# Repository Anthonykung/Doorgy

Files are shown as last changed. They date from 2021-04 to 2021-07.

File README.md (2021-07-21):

# Doorgy

A smart pet door for your smart home

***APLHA RELEASE WARNING*** Currently Under Development - This is not production ready!

Estimated Time of Completion: May 28, 2021

This is an open source academic group project for ECE 342 Junior Design at Oregon State University.

# Contents
- [Doorgy](#doorgy)
- [Contents](#contents)
  - [Overview](#overview)
  - [Prerequisite](#prerequisite)
    - [Doorgy Installation Package](#doorgy-installation-package)
    - [Required Software](#required-software)
    - [Configuring Doorgy Service](#configuring-doorgy-service)
      - [From GitHub](#from-github)
      - [From NPM](#from-npm)
  - [Install](#install)
    - [Physical Installation](#physical-installation)
    - [System Configuration](#system-configuration)
  - [License](#license)

## Overview

Doorgy is a smart pet door for your smart home. Control your pet door with nothing but your phone! Automated pet detection and door opening, say open sesame. Plug and play, no code required!

## Prerequisite

This project requires the Doorgy Installation Package that comes with the specific components require for the installation. Schematics of these components are available should you choose to create your own. You will not be able to proceed without these components.

Doorgy is part of the Doorgy Project, all parts of Doorgy Project are required to operate.

| Project | Registry | Repository |
| --- | --- | --- |
| Doorgy | [https://www.npmjs.com/package/doorgy](https://www.npmjs.com/package/doorgy) | [https://github.com/Anthonykung/Doorgy](https://github.com/Anthonykung/Doorgy) |
| Doorgy Server | | [https://github.com/Anthonykung/Doorgy-Server](https://github.com/Anthonykung/Doorgy-Server) |
| Doorgy App | | [https://github.com/Anthonykung/Doorgy-App](https://github.com/Anthonykung/Doorgy-App) |

### Doorgy Installation Package

- 1x Doorgy Printed Circuit Board
- 1x Raspberry Pi Zero WH
- 1x 16GB Doorgy Service Micro SD Card
- 2x HC-SR501
- 1x Doorgy LED Assembly
- 2x Servo Motors with Extended Arms
- 1x Battery Pack
- 1x Micro USB Power Supply
- 1x Doorgy Exterial Top/Bottom/Left/Right Frame
- 1x Doorgy Interial Top/Bottom/Left/Right Frame (Top frame comes with Circuit Housing)
- 1x Doorgy Door
- 1x Doorgy Door Connector & Doorgy Servo Connector
- 4x 1 Inch Doorgy Frame Screw
- 2x 1/4 Inch Doorgy Housing Screw
- 2x 1/4 Inch Doorgy Door Screw

### Required Software

If you have the Doorgy Service Micro SD Card, these has already been installed and configured.

If you do not have a Doorgy Service Micro SD Card, you will need a Micro SD Card with Raspbian Lite installed, more information available on [https://www.raspberrypi.org/documentation/installation/installing-images/](https://www.raspberrypi.org/documentation/installation/installing-images/). Once you have a Micro SD Card with Raspbian Lite installed, you can use the `doorgy-init.sh` located in `resources` folder of this repo to install the require softwares.

- UFW
- Fail2ban
- Git
- Node.js
- NPM
- Express.js
- mongoDB

Note: You should always secure your Raspberry Pi, Doorgy Service Micro SD Card will have security enabled by default. If you are using `doorgy-init.sh`, only firewall will be enabled. You will need to setup your Raspbian user and configure Fail2ban manually, more information available on [https://www.raspberrypi.org/documentation/configuration/security.md](https://www.raspberrypi.org/documentation/configuration/security.md)

### Configuring Doorgy Service

If you have the Doorgy Service Micro SD Card, these has already been installed and configured.

#### From GitHub

```
git clone https://github.com/Anthonykung/Doorgy.git
sudo npm install
sudo systemctl enable doorgy
```

If the installation fail, you can use `sudo npm run install` to try again. Sudo is required for all operations.

Once the service has been successfully configured, you can either start or reboot to start the service.

#### From NPM

```
mkdir ~/Doorgy
cd ~/Doorgy
sudo npm install doorgy
sudo systemctl enable doorgy
```

If the installation fail, you can use `sudo npm run install` to try again. Sudo is required for all operations.

Once the service has been successfully configured, you can either start or reboot to start the service.

## Install

This assume you have the Doorgy Installation Package and met all the prerequisites, if not please check that you have met the prerequisites before continuing.

### Physical Installation

1. Remove the door and place it on a table
2. Using the Doorgy Interial Frame, mark all 4 sides of the frame for cutting
3. Leave at least 3 inches of space on each side and 4 inches on the bottom
4. Cut the door on the marked location, this should give you a rectangular hole for the Doorgy Interial Frame
5. Place the Doorgy Interial Frame to the door (facing the inside), this should give you a tight fit
6. Place the Doorgy Exterial Frame on the other side overlapping the Doorgy Interial Frame
7. Using the 1 Inch Doorgy Screws, screw the Interial Fram to the Exterial Frame (the hole is located on the Interial Frame)
8. Using the 1/4 Inch Doorgy Screws, secure the circuit housing to the door (you will need to dril a 1/4 inch hole on the door)
9. On the exterial side, push the Doorgy Door in place with the hook on the top facing inside, secure it with the 1/4 inch screw to the frame
10. Attach the servo arm to the hook on top of the door, do not touch the servo arm on the left
11. Plugin the Micro USB power cable or attach 4x AAA batteries (not included) to the battery pack
12. Press the power up button and you are good to go! (Remember to tidy up the power cable so it doesn't get pulled out!)

### System Configuration

1. Install the Doorgy app on your smartphone
2. Open the Doorgy app and create an account
3. Setup WiFi connection with Raspberry Pi and run `npm run config`
4. Finish configuring Doorgy with the app
5. Once configuration is complete, follow the display to restart Doorgy (this is only needed during initial system configuration)
6. Enjoy your awesome new smart pet door!

## License

Copyright 2021 Doorgy Project Group

Licensed under the Apache License, Version 2.0 (the "License"); you may not use this file except in compliance with the License. You may obtain a copy of the License at

    http://www.apache.org/licenses/LICENSE-2.0

Unless required by applicable law or agreed to in writing, software distributed under the License is distributed on an "AS IS" BASIS, WITHOUT WARRANTIES OR CONDITIONS OF ANY KIND, either express or implied. See the License for the specific language governing permissions and limitations under the License.

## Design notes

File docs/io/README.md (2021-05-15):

# ECE 342 Pet Door Project - Doorgy

Doorgy - Smart Pet Door for your home, connected right to your phone. Hidden surprise included.

Created by Anthony Kung <hi@anth.dev> (https://anth.dev)

## Contents

- [ECE 342 Pet Door Project - Doorgy](#ece-342-pet-door-project---doorgy)
  - [Contents](#contents)
  - [Overview](#overview)
  - [Schematic](#schematic)
  - [Mechanical Drawing](#mechanical-drawing)
    - [Raspberry Pi Zero](#raspberry-pi-zero)
    - [HC-SR501](#hc-sr501)
    - [5mm LED](#5mm-led)
  - [Code](#code)
    - [Structure](#structure)
      - [Entire Service Package](#entire-service-package)
      - [Service File](#service-file)
    - [Primary Program Executable](#primary-program-executable)
    - [Installer](#installer)
    - [Service Scheduler](#service-scheduler)
  - [Block Diagrams](#block-diagrams)
    - [Overall System](#overall-system)
    - [Black Box Diagram](#black-box-diagram)
    - [Block Diagram](#block-diagram)
  - [Interface Definition](#interface-definition)
  - [Bill of Material](#bill-of-material)

## Overview

This portion of the project includes IR motion sensors and 5mm LEDs.

The IR sensors (HC-SR501) are used to detect pet movements from inside and outside the door. The IR sensor will be used to send the control signal to a single board computer (Raspberry Pi Zero WH) to be processed and activate the servo motors to open the door.

The 5mm LEDs are used to indicate the condition of the system. A green LED indicates the system is operating with sufficient power. A blue LED is used to indicate network connectivity. A red LED is used to indicate if the door has been locked. And a yellow LED is used to report errors. A 5mm LED has a current rating of 20mA, to protect the LED from the Raspberry Pi 5V voltage supply, a 250Ω resistor is required for each of them. This value is calculated by the formula ***V = IR*** where the resistor value can be found by dividing the voltage (5V) by the current (20mA) which gives 250Ω.

## Schematic

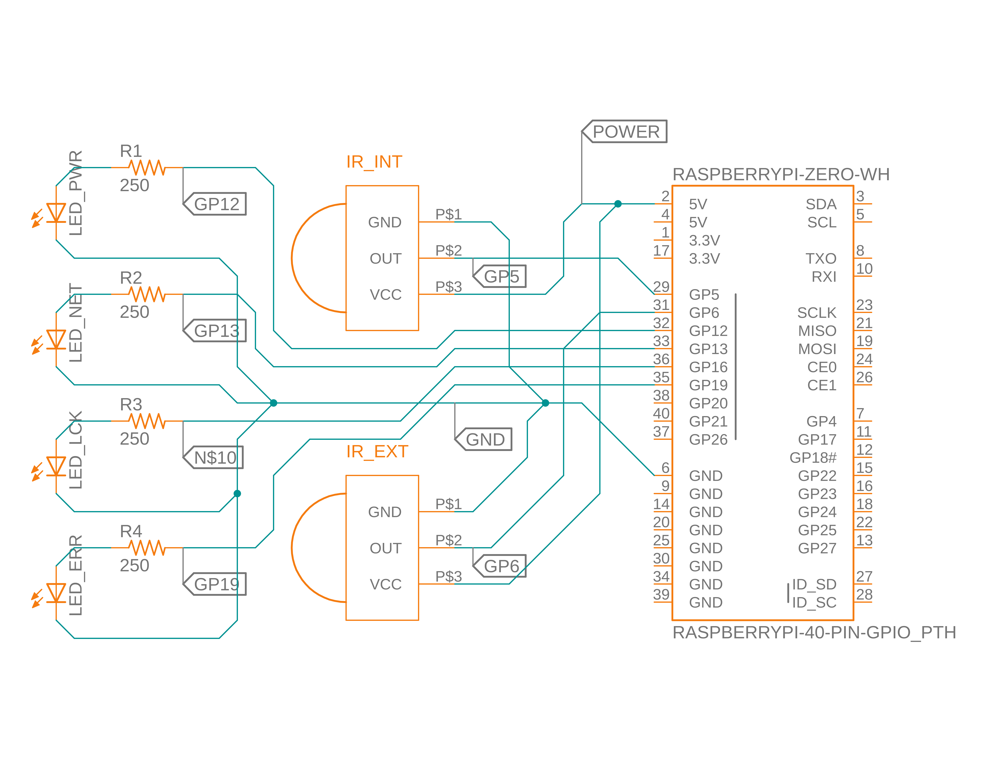
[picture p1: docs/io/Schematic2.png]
Schematic


## Mechanical Drawing

### Raspberry Pi Zero

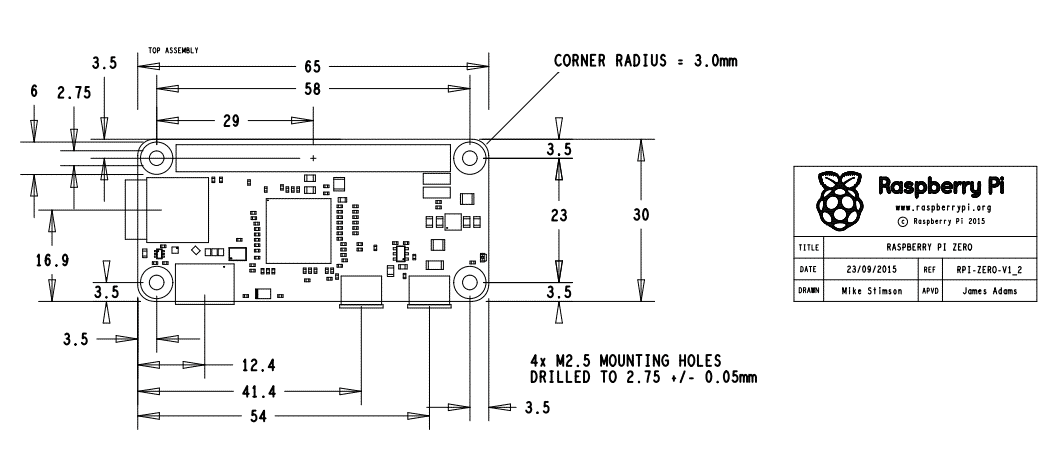
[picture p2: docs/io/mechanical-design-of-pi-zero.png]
Raspberry Pi Zero


### HC-SR501

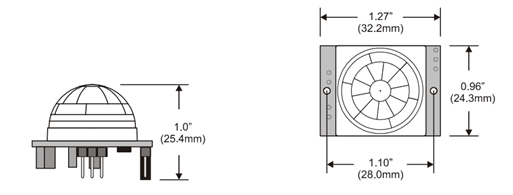
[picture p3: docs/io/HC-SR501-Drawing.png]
HC-SR501


### 5mm LED

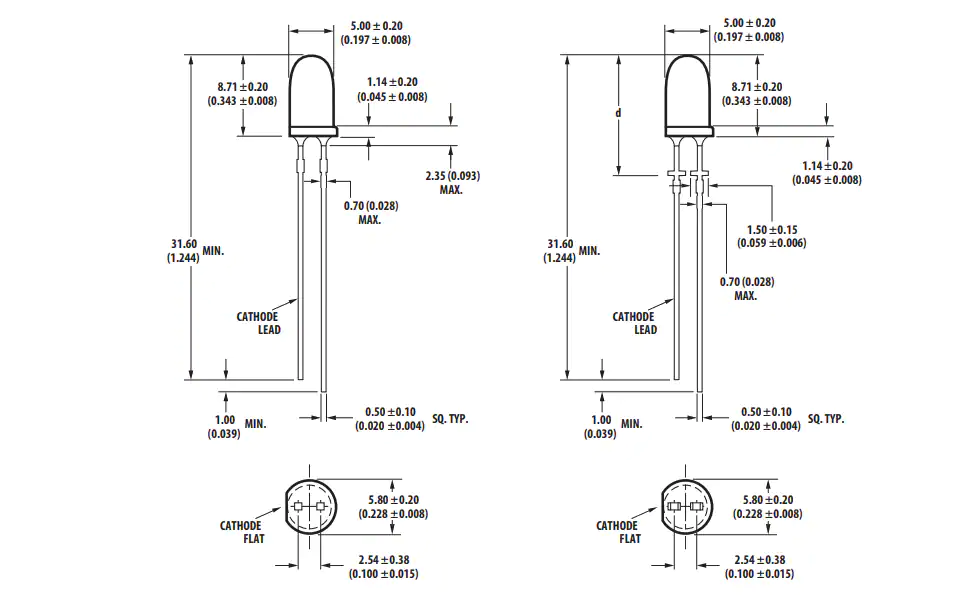
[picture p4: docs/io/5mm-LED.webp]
5mm LED


## Code

### Structure

#### Entire Service Package

```
/usr/local/src/
├── README.md
├── doorgy.js
├── package.json
└── resources/
    ├── installer.js
    ├── doorgy.service
    ├── doorgy-init.sh
    └── anthonian.js
```

#### Service File

```
/etc/systemd/services/
└── doorgy.service
```

### Primary Program Executable

```javascript
/**
 *
 * @description Doorgy - Smart Pet Door.
 * @file        doorgy.js
 * @link        https://doorgy.anth.dev
 * @license     Apache-2.0
 * @author      Anthony Kung <hi@anth.dev>
 * @since       1.0.0
 * @version     1.2.8
 *
 */

// Include Packages
const gpio = require('onoff').Gpio;
const fs = require('fs');
const anth = require('./resources/anthonian.js');
const { execSync, spawn } = require('child_process');
const http = require('http');

anth.anthdev();
anth.print('msg', 'Starting Doorgy Service');

// Define Global Constant
const server = 'doorgy.anth.dev';

// Define Global Variable
let ctrlSig = 1;
let printNum = 0;

// Define IR gpio
const IR_INT = new gpio(5, 'in', 'both');
const IR_EXT = new gpio(6, 'in', 'both');

// Define Buttons
const KILL = new gpio(20, 'in', 'rising', {debounceTimeout: 100});
const PSH_BTN2 = new gpio(21, 'in', 'rising', {debounceTimeout: 100});
const PSH_BTN3 = new gpio(26, 'in', 'rising', {debounceTimeout: 100});

// Define LED gpio
const LED_PWR = new gpio(12, 'out');
const LED_NET = new gpio(13, 'out');
const LED_LCK = new gpio(16, 'out');
const LED_ERR = new gpio(19, 'out');

anth.print('suc', 'GPIO Defined');
LED_PWR.writeSync(0);
LED_NET.writeSync(0);
LED_LCK.writeSync(0);
LED_ERR.writeSync(0);

// Turn on power indicator
LED_PWR.writeSync(1);

/**
 * Interial IR Function.
 *
 * @access private
 * @param  {*} err
 * @param  {*} value
 *
 * @memberof IR_INT
 */
IR_INT.watch((err, value) => {
  if (err) {
    throw err;
  }
  else if (value) {
    // Inform Servo Unit montion is detected
    console.log('IR_INT Sense', value);
    LED_ERR.writeSync(1);
  }
  else {
    // Inform Servo Unit no motion is detected
    console.log('IR_INT Not Sense', value);
    LED_ERR.writeSync(0);
  }
});

/**
 * Exterial IR Function.
 *
 * @access private
 * @param  {*} err
 * @param  {*} value
 *
 * @memberof IR_EXT
 */
IR_EXT.watch((err, value) => {
  if (err) {
    throw err;
  }
  else if (value) {
    // Inform Servo Unit montion is detected
    console.log('IR_EXT Sense', value);
    LED_ERR.writeSync(1);
  }
  else {
    // Inform Servo Unit no motion is detected
    console.log('IR_EXT Not Sense', value);
    LED_ERR.writeSync(0);
  }
});

/**
 * LED_LCK Test Function.
 *
 * @access private
 * @param  {*} err
 * @param  {*} value
 *
 * @memberof PSH_BTN2
 */
PSH_BTN2.watch((err, value) => {
  if (err) {
    throw err;
  }
  else if (value) {
    // Turn on Lock indicator
    console.log('Lock Sense', value);
    LED_LCK.writeSync(1);
    setTimeout(() => {
      console.log('Lock Release');
      LED_LCK.writeSync(0);
    }, 2000);
  }
  else {
    // Turn off Lock indicator
    console.log('Lock Not Sense', value);
    LED_LCK.writeSync(0);
  }
});

/**
 * LED_ERR Test Function.
 *
 * @access private
 * @param  {*} err
 * @param  {*} value
 *
 * @memberof PSH_BTN3
 */
PSH_BTN3.watch((err, value) => {
  if (err) {
    throw err;
  }
  else if (value) {
    // Turn on Lock indicator
    LED_ERR.writeSync(1);
  }
  else {
    // Turn off Lock indicator
    LED_ERR.writeSync(0);
  }
});

/**
 * Termination Cleanup Function.
 *
 * @name   clean
 * @access private
 * @param  {*} err
 * @param  {*} value
 */
function clean() {
  clearInterval(netCheck);
  LED_PWR.writeSync(1);
  LED_NET.writeSync(0);
  LED_LCK.writeSync(0);
  LED_ERR.writeSync(0);
  IR_INT.unexport();
  IR_EXT.unexport();
  LED_PWR.unexport();
  LED_NET.unexport();
  LED_LCK.unexport();
  LED_ERR.unexport();
}

/**
 * Interruption Control.
 *
 * Free resources and exit if interrupted.
 *
 * @listens SIGINT
 * @access private
 * @memberof process
 */
process.on('SIGINT', () => {
  clean();
  process.exit(0);
});

/**
 * Termination Control.
 *
 * Free resources and exit if terminated.
 *
 * @listens SIGTERM
 * @access private
 * @memberof process
 */
process.on('SIGTERM', () => {
  clean();
  process.exit(0);
});

/**
 * Locking Control.
 *
 * Listern for Locking Mechnism.
 *
 * @listens message
 * @access private
 * @memberof process
 */
process.on('message', message => {
  let comm = JSON.parse(message);
  if (comm.Lock.status == 1) {
    // Turn on Lock indicator
    LED_LCK.writeSync(1);
  }
  else {
    // Turn off Lock indicator
    LED_LCK.writeSync(0);
  }
});

anth.print('msg', 'Starting Operation');

/**
 * Network Check Function.
 *
 * Check for network connection.
 *
 * @name   checkNetwork
 * @access private
 * @param  {string} server
 */
function checkNetwork(server) {
  let  options = {
    host: server,
    path: '/'
  };
  http.get(options, (res) => {
    if (!printNum) {
      anth.print('suc', 'Connection Established');
      printNum++;
    }
    LED_NET.writeSync(1);
  }).on('error', function(error) {
    console.error('Error Detected:', error);
    LED_NET.writeSync(0);
    LED_ERR.writeSync(1);
    anth.print('err', 'Unable to communicate with server');
  });
}

let netCheck = setInterval(checkNetwork(server), 100);

/**
 * Kill Function.
 *
 * Initiate graceful shutdown
 *
 * @access private
 * @param  {*} err
 * @param  {*} value
 *
 * @memberof KILL
 */
KILL.watch((err, value) => {
  if (err) {
    throw err;
  }
  else if (value) {
    clean();
    let cmd = execSync('shutdown -h now');
  }
  else {
    console.error('Error Detected:', error);
    LED_ERR.writeSync(1);
    anth.print('err', 'Unable to shutdown the server');
  }
});
```

### Installer

```js
#!/usr/bin/env node

/*******************************************
 *                                         *
 * Name: installer.js                      *
 * Description: Doorgy Installation Helper *
 * Date: April 26, 2021                    *
 * Created by: Anthony Kung                *
 * Author URL: https://anth.dev            *
 * License: Apache-2.0 (See LICENSE.md)    *
 *                                         *
 *******************************************/

// Just to be nice
'use strict';

// Modules
const { exec, spawn } = require('child_process');
const anth = require('./anthonian.js');
const fs = require("fs");
const path = require('path');
const fse = require('fs-extra');

anth.print('msg', 'Checking Directory Location');

if (__dirname != '/usr/local/src/doorgy') {
  anth.print('msg', 'Relocation required, relocating...');
  try {
    fse.copySync(__dirname + '/../', '/usr/local/src/doorgy');
    anth.print('suc', 'Relocation Success');
  } catch (err) {
    anth.print('err', 'Unable to move directory');
  }
}
anth.print('suc', 'Directory Check Completed');

anth.print('msg', 'Checking Service Location');

if (!fs.existsSync('/etc/systemd/system/doorgy.service')) {
  anth.print('msg', 'Service not found, adding service...');
  try {
    fse.copySync(path.join(__dirname, 'doorgy.service'), '/etc/systemd/system/doorgy.service');
    anth.print('suc', 'Service Added Successfully');
  } catch (err) {
    anth.print('err', 'Unable to move file');
  }
}
anth.print('suc', 'Service Check Completed');

anth.print('suc', 'Doorgy Installation Completed');
anth.print('msg', ['Start the service using', anth.pink, 'sudo npm start', anth.blue, 'or', anth.pink, 'sudo systemctl start doorgy.service', anth.blue, 'sudo is required for system services']);
```

### Service Scheduler

```
[Unit]
Description=Doorgy Service Agent
Documentation=https://github.com/Anthonykung/Doorgy

[Service]
ExecStart=/usr/bin/node /usr/local/src/doorgy/doorgy.js
WorkingDirectory=/usr/local/src/doorgy
StandardOutput=inherit
StandardError=inherit
Restart=always
User=root

[Install]
WantedBy=multi-user.target
```

## Block Diagrams

### Overall System

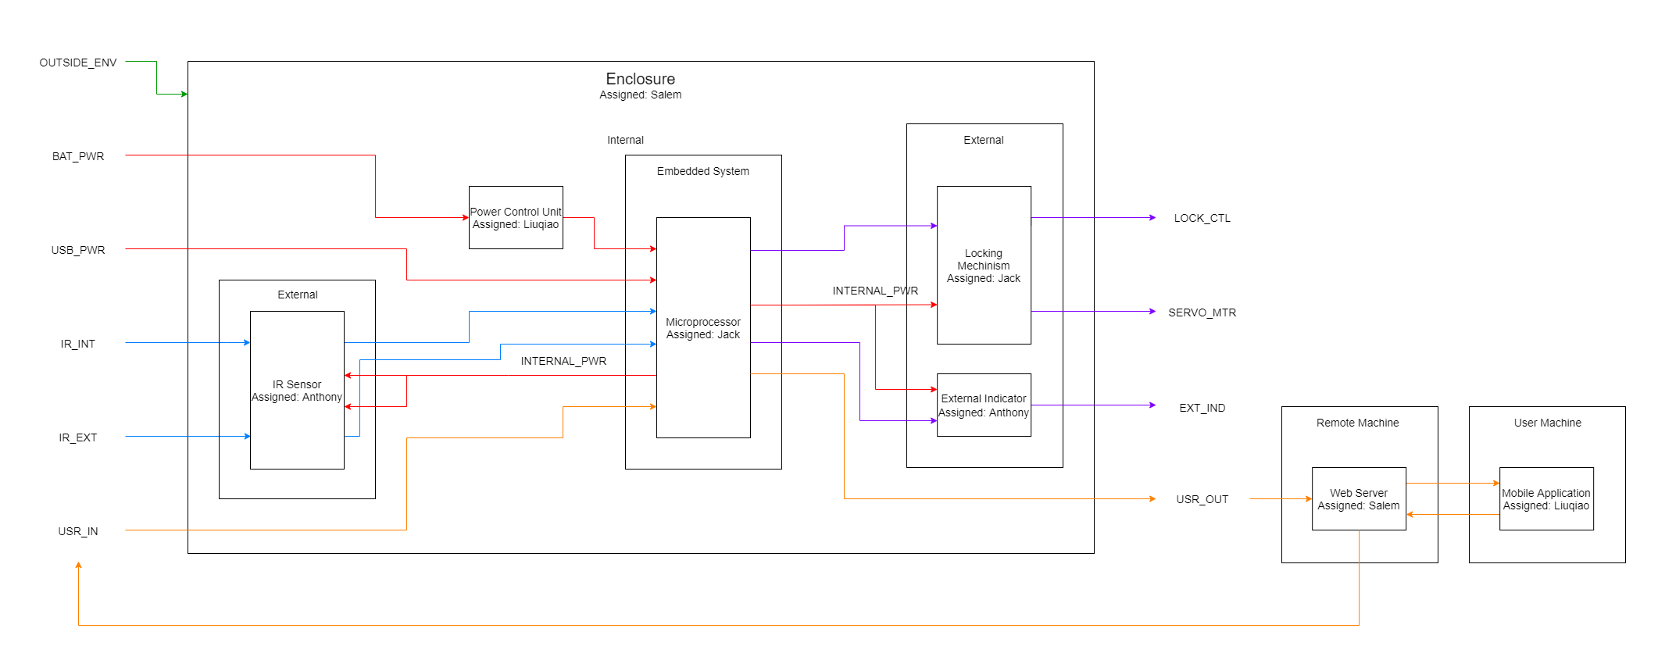
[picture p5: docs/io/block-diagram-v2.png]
Overall Block Diagram


### Black Box Diagram
Black Box Diagram

### Block Diagram
Block Diagram

## Interface Definition

| Name | Type | Definition |
| --- | --- | --- |
| BAT_PWR  | DC Power | <ul><li>Voltage: 5.1V</li><li>Current: 1.2A</li></ul> |
| USB_PWR  | DC Power | <ul><li>Voltage: 5.1V</li><li>Current: 1.2A</li></ul> |
| POWER | DC Power | <ul><li>Voltage: 5.0V</li><li>Current: 1.2A</li></ul> |
| IR_INT | Analog Signal | <ul><li>Voltage: DC 5V</li><li>Minimium Range: 1m</li></ul> |
| IR_EXT | Analog Signal | <ul><li>Voltage: DC 5V</li><li>Minimium Range: 1m</li></ul> |
| COMM_IN  | Data | Format: JSON Object |
| COMM_OUT | Data | Format: JSON Object |
| LED_PWR  | Analog Signal | <ul><li>Voltage: 5.0V</li><li>Current: 20mA</li></ul> |
| LED_NET  | Analog Signal | <ul><li>Voltage: 5.0V</li><li>Current: 20mA</li></ul> |
| LED_LCK  | Analog Signal | <ul><li>Voltage: 5.0V</li><li>Current: 20mA</li></ul> |
| LED_ERR  | Analog Signal | <ul><li>Voltage: 5.0V</li><li>Current: 20mA</li></ul> |

## Bill of Material

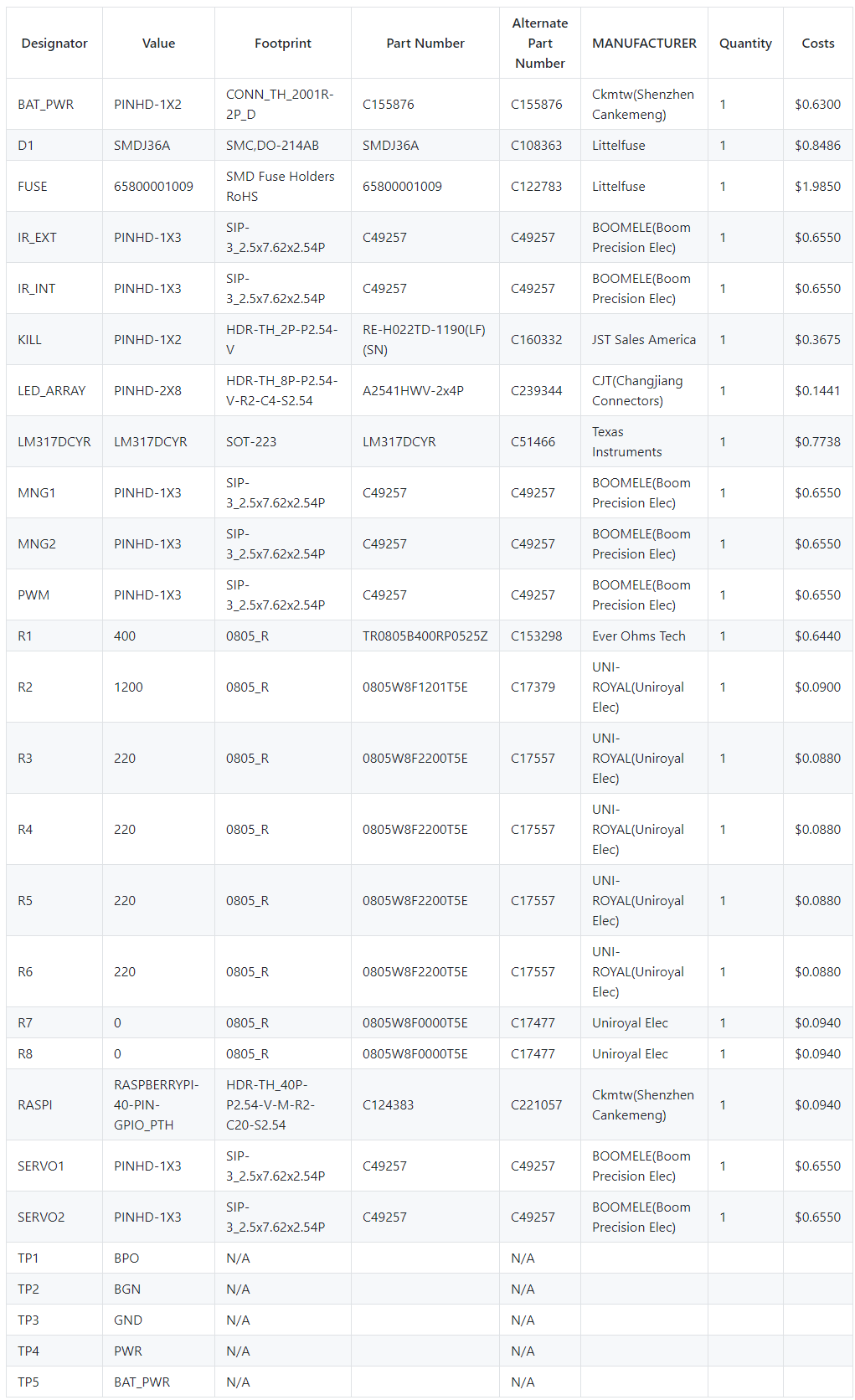
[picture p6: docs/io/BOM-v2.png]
BOM


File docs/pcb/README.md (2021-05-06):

# Doorgy PCB

The Doorgy PCB integrates Raspberry Pi Zero WH with the Doorgy Frame and Hardwares.

Schematics, PCB Layout and Gerber Files are open source and freely available on this directory.

BOM and CPL used to construct Doorgy PCB on JLCPCB is also available on this directory.

- [Doorgy PCB](#doorgy-pcb)
  - [Gerber Files](#gerber-files)
  - [BOM](#bom)
  - [CPL](#cpl)
  - [PCB](#pcb)
  - [Schematic](#schematic)
  - [Layout](#layout)

## Gerber Files

Current version: v33

Gerber files of the Doorgy PCB is located at [./Doorgy-PCB_2021-05-04-v33.zip](./Doorgy-PCB_2021-05-04-v33.zip)

## BOM

The BOM is currently only available in Microsoft Excel format and is located at [./Doorgy-PCB-BOM.xlsx](./Doorgy-PCB-BOM.xlsx)

## CPL

The CPL is currently only available in Microsoft Excel format and is located at [./Doorgy-PCB-CPL.xlsx](./Doorgy-PCB-CPL.xlsx)

## PCB

This is a illustration of a constructed Doorgy PCB Layout Version 32

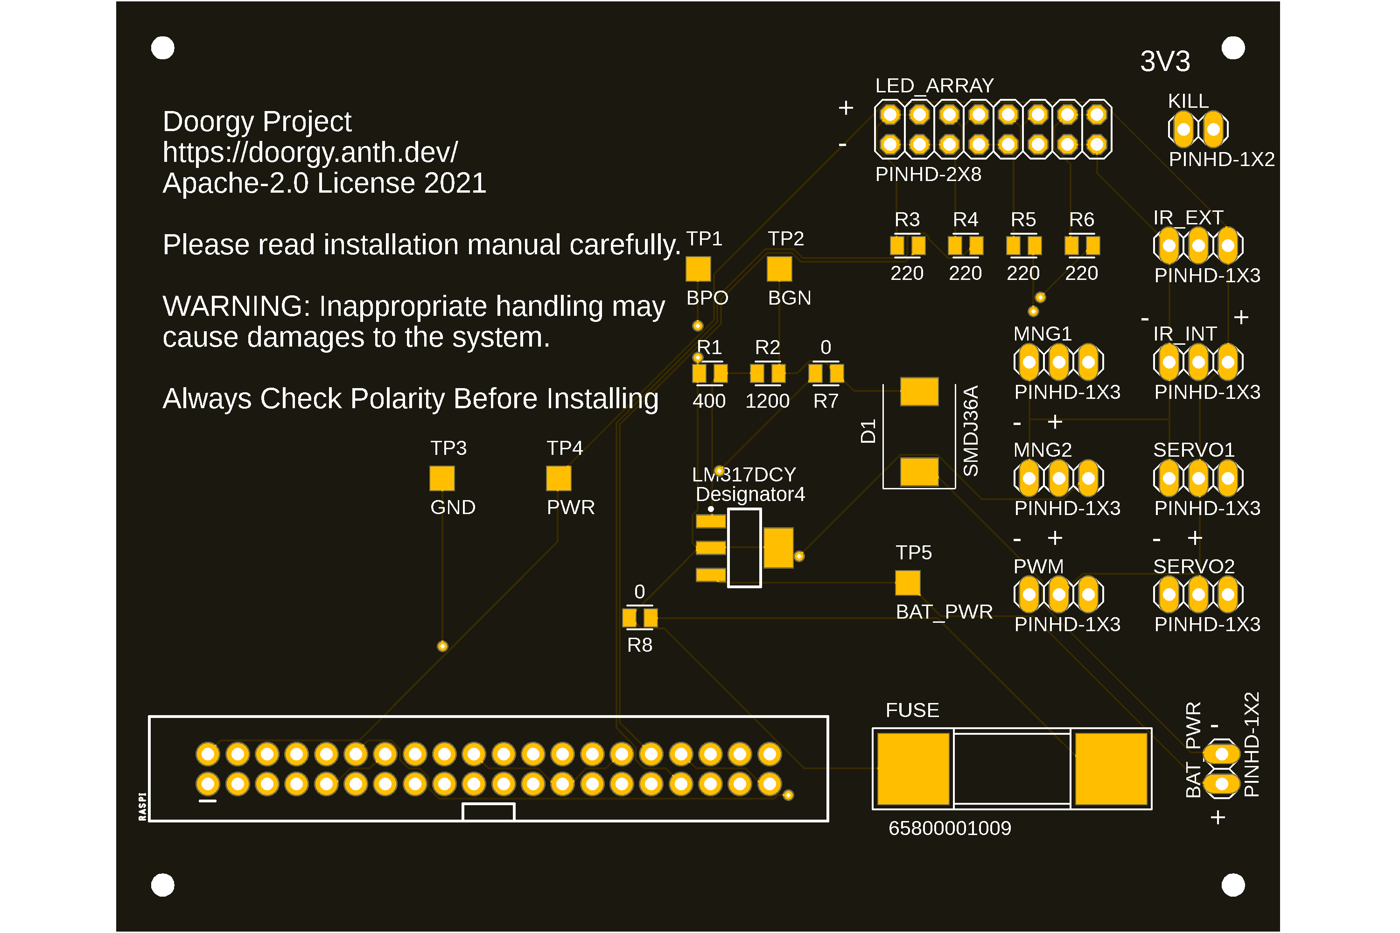
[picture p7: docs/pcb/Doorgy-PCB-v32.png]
Doorgy PCB v32


## Schematic

This is the schematic of Doorgy PCB Schematic Version 22, note that resistor values have been changed to accomodate the parts available at JLCPCB.

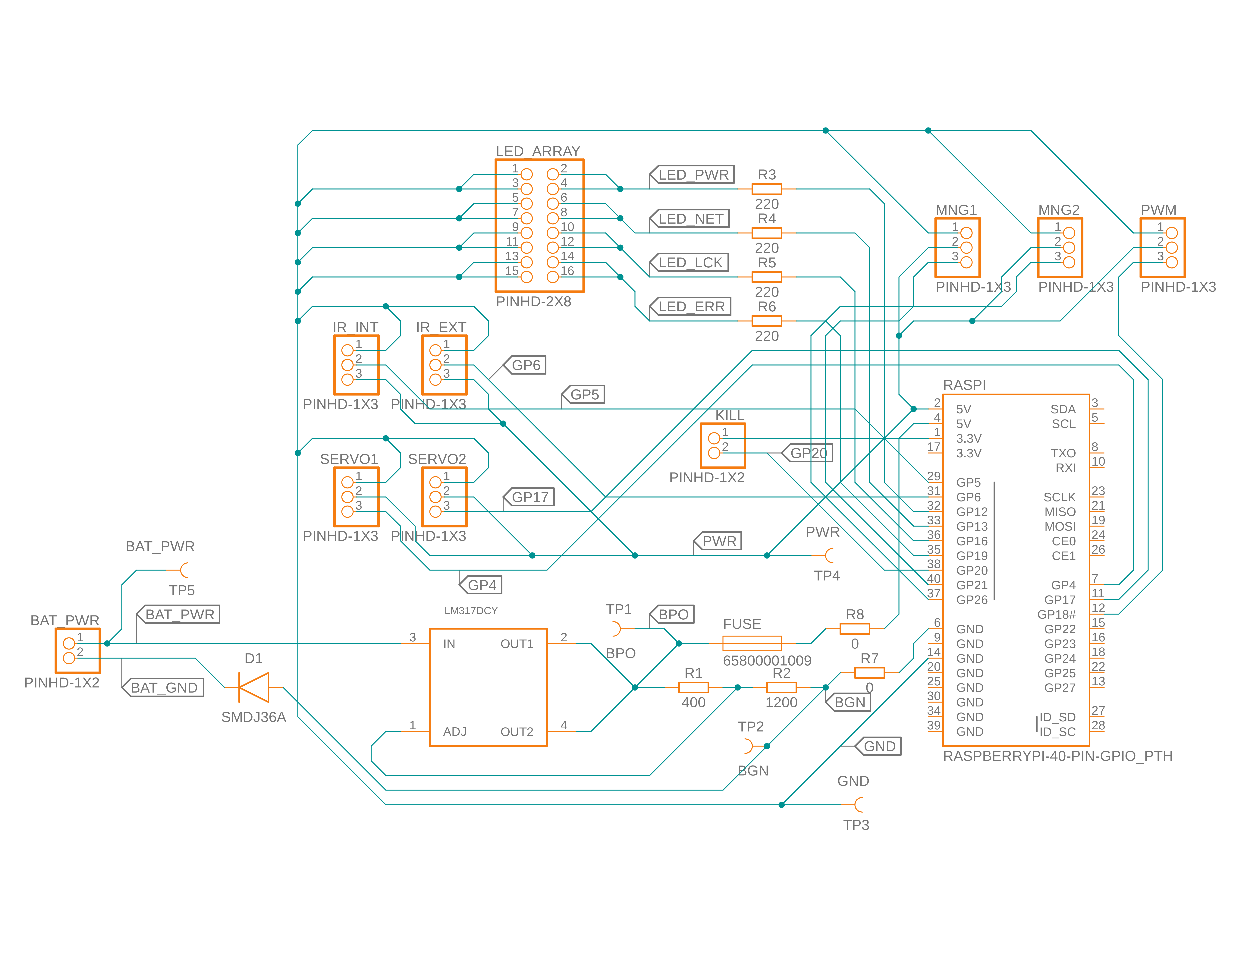
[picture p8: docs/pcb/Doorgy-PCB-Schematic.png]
Schematic v22


## Layout

This is the routing layout of Doorgy PCB Layout Version 32.

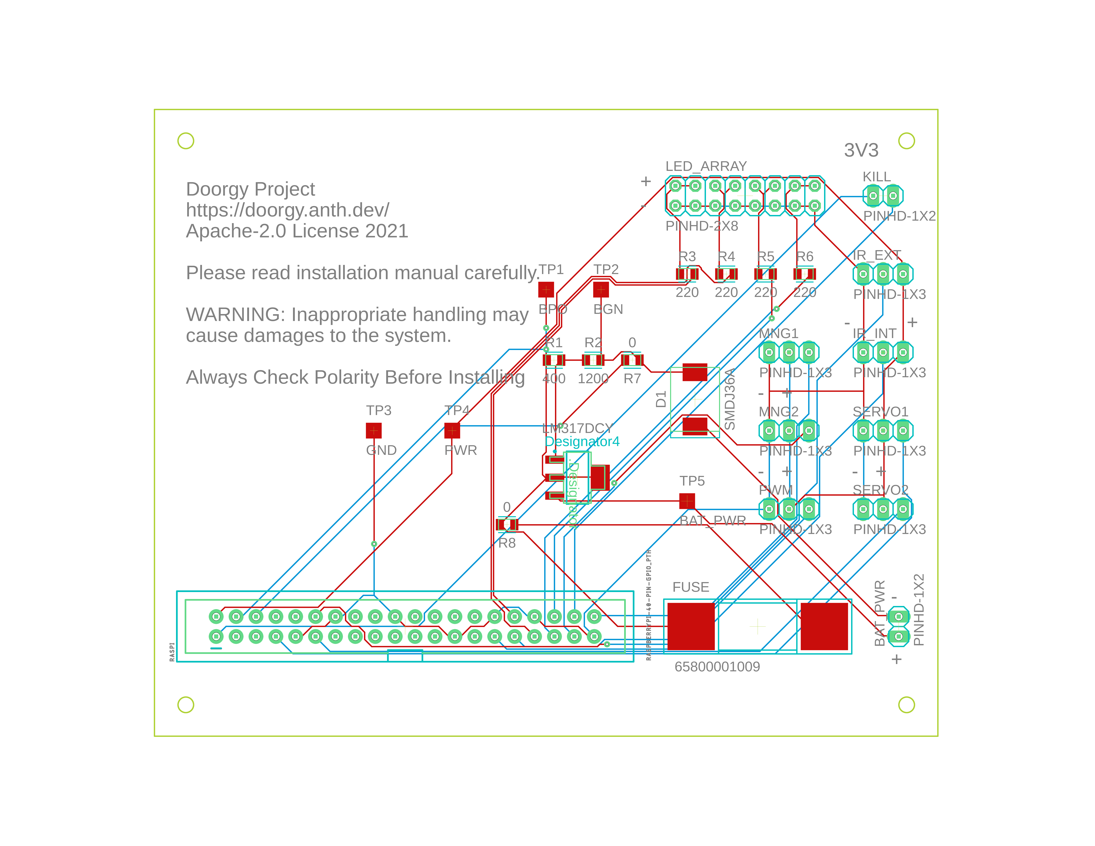
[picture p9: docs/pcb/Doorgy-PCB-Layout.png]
Layout v32


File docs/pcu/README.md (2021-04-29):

# Power Control Unit

This block is managed by Liuqiao Song

## Contents
- [Power Control Unit](#power-control-unit)
  - [Contents](#contents)
  - [Schematic](#schematic)
  - [Bill of Material](#bill-of-material)
  - [Additional](#additional)
    - [Voltage Monitoring](#voltage-monitoring)

## Schematic

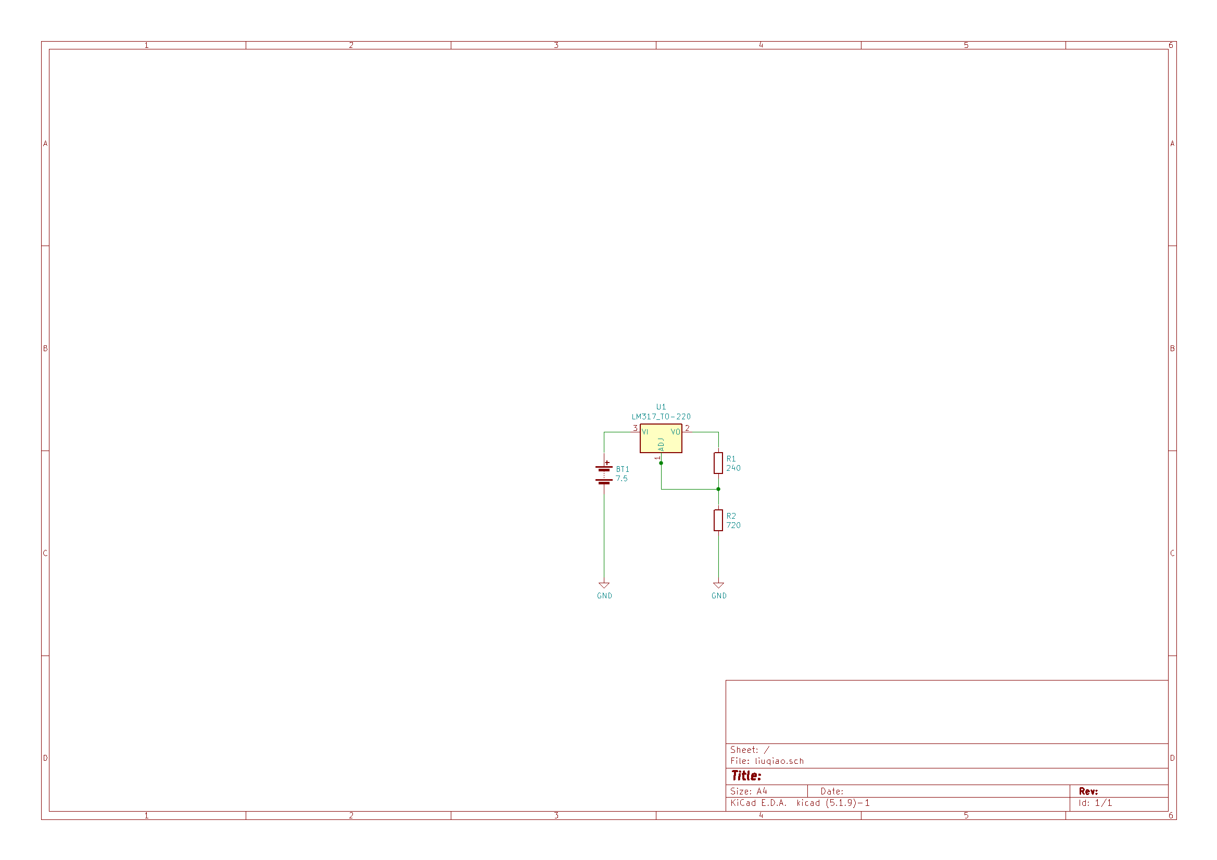
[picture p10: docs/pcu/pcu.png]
Power Control Unit


## Bill of Material

| Quantity | Name |
| --- | --- |
| 1 | LM317 |
| 1 | 240 ohm R |
| 1 | 720 ohm R |
| 1 | 5 pack AA battery |

## Additional

This section is added by Anthony Kung

### Voltage Monitoring

An INA 169 will be used to monitor voltage and provide battery statistics to the Raspi. AA battery operates at 1.5V and became inoperatable at around 1.2V.

[INA169 Datasheet](https://www.ti.com/lit/ds/symlink/ina169.pdf)

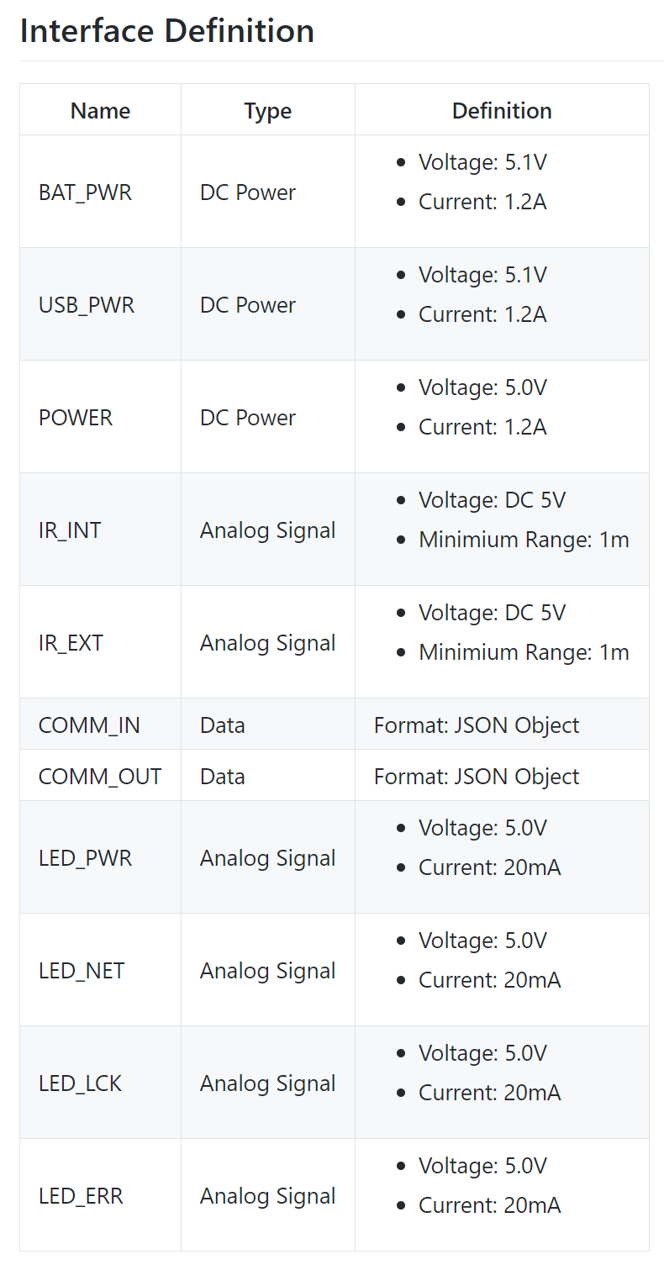
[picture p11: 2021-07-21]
docs/overview/Screenshot 2021-05-28 204917.png

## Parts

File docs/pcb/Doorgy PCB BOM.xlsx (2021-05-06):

Comment | Designator | Footprint | LCSC Part #（optional）
PINHD-1X2 | BAT_PWR | CONN_TH_2001R-2P_D | C155876
SMDJ36A | D1 | SMC,DO-214AB | C108363
65800001009 | FUSE | SMD Fuse Holders RoHS | C122783
PINHD-1X3 | IR_EXT | SIP-3_2.5x7.62x2.54P | C49257
PINHD-1X3 | IR_INT | SIP-3_2.5x7.62x2.54P | C49257
PINHD-1X2 | KILL | HDR-TH_2P-P2.54-V | C160332
PINHD-2X8 | LED_ARRAY | HDR-TH_8P-P2.54-V-R2-C4-S2.54 | C239344
LM317DCYR | LM317DCYR | SOT-223 | C51466
PINHD-1X3 | MNG1 | SIP-3_2.5x7.62x2.54P | C49257
PINHD-1X3 | MNG2 | SIP-3_2.5x7.62x2.54P | C49257
PINHD-1X3 | PWM | SIP-3_2.5x7.62x2.54P | C49257
400 | R1 | 0805_R | C153298
1200 | R2 | 0805_R | C17379
220 | R3 | 0805_R | C17557
220 | R4 | 0805_R | C17557
220 | R5 | 0805_R | C17557
220 | R6 | 0805_R | C17557
0 | R7 | 0805_R | C17477
0 | R8 | 0805_R | C17477
RASPBERRYPI-40-PIN-GPIO_PTH | RASPI | HDR-TH_40P-P2.54-V-M-R2-C20-S2.54 | C221057
PINHD-1X3 | SERVO1 | SIP-3_2.5x7.62x2.54P | C49257
PINHD-1X3 | SERVO2 | SIP-3_2.5x7.62x2.54P | C49257
Leave Empty | TP1 | N/A | N/A
Leave Empty | TP2 | N/A | N/A
Leave Empty | TP3 | N/A | N/A
Leave Empty | TP4 | N/A | N/A
Leave Empty | TP5 | N/A | N/A

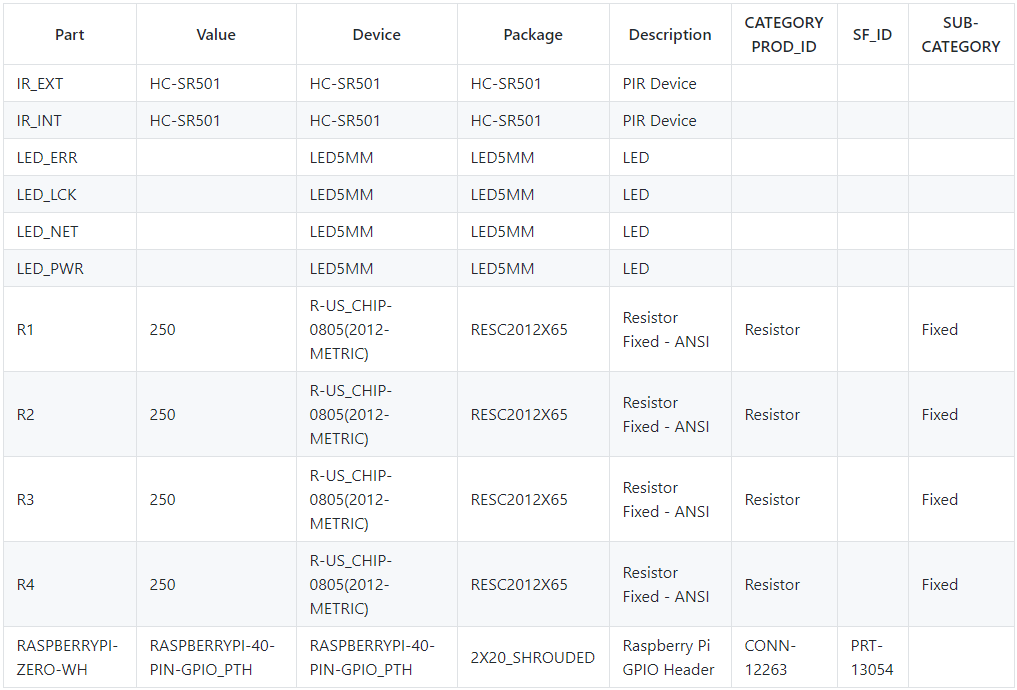
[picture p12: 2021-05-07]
docs/io/BOM.png

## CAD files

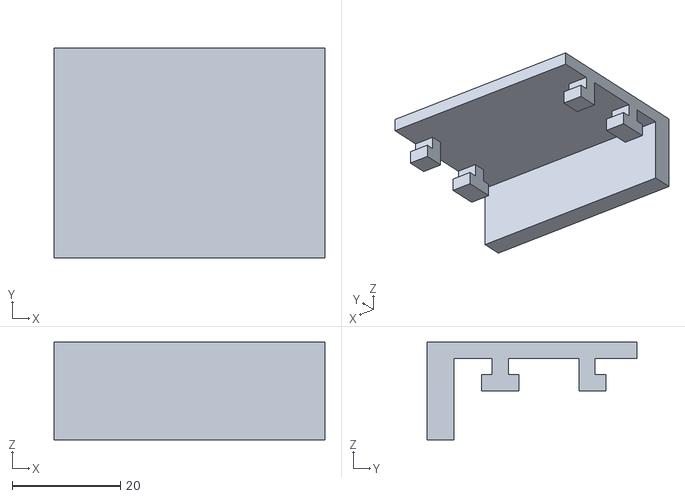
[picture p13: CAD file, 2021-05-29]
Doorgy Physical STL/Doorgy Exterial Top Cover.stl
50.0 x 38.8 x 18.0

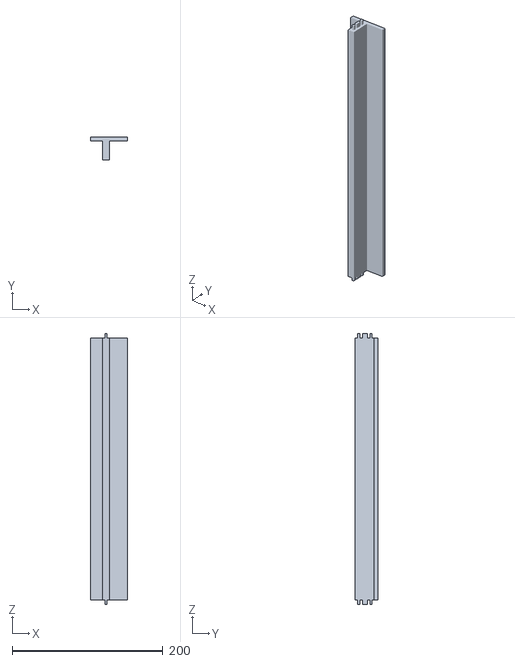
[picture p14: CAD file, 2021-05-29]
Doorgy Physical STL/Doorgy Exterial Left Frame.stl
49.0 x 30.4 x 359.0

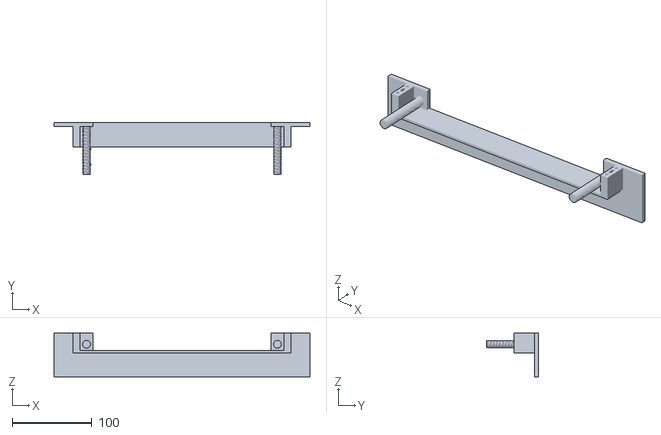
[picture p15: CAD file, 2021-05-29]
Doorgy Physical STL/Doorgy Exterial Bottom Frame.stl
322.0 x 65.0 x 55.0

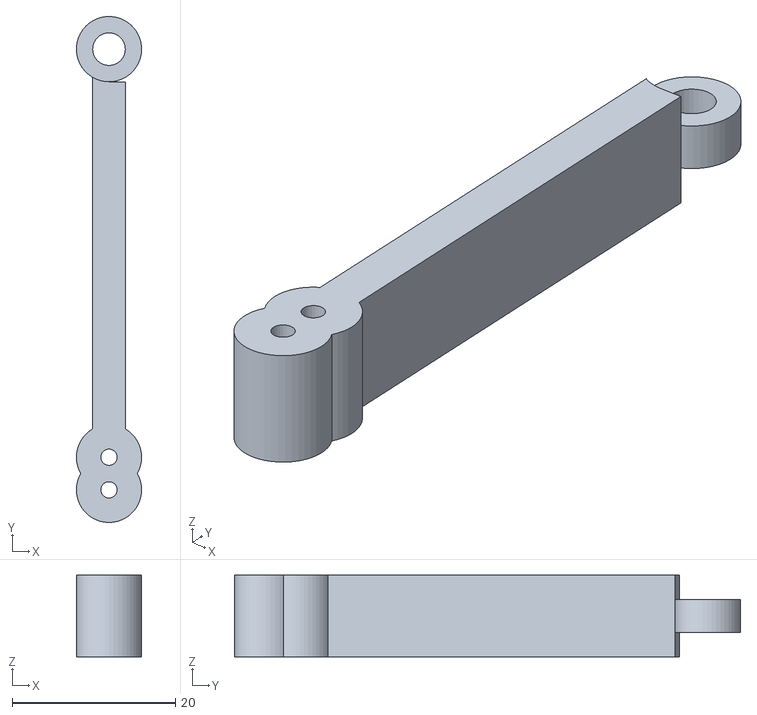
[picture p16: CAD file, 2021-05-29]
Doorgy Physical STL/Doorgy Servo Connector.stl
8.00 x 62.0 x 10.0

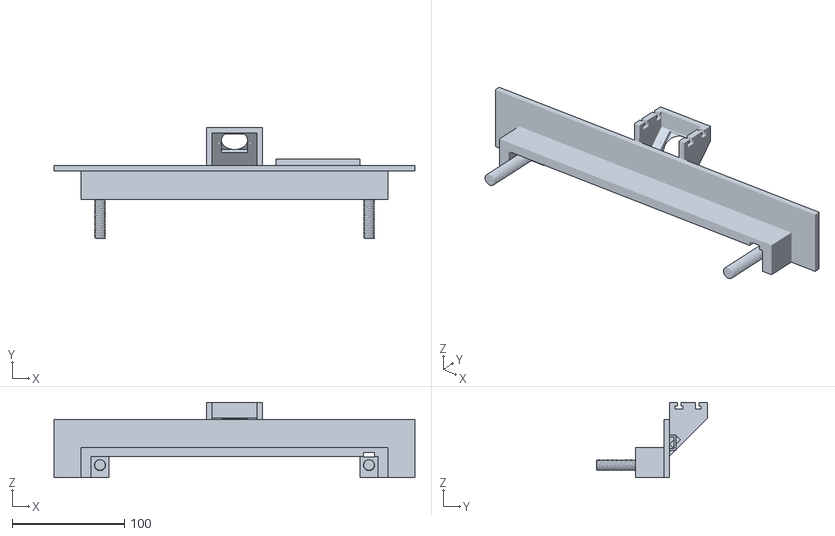
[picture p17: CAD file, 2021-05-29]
Doorgy Physical STL/Doorgy Exterial Top Frame.stl
322.0 x 98.9 x 67.0

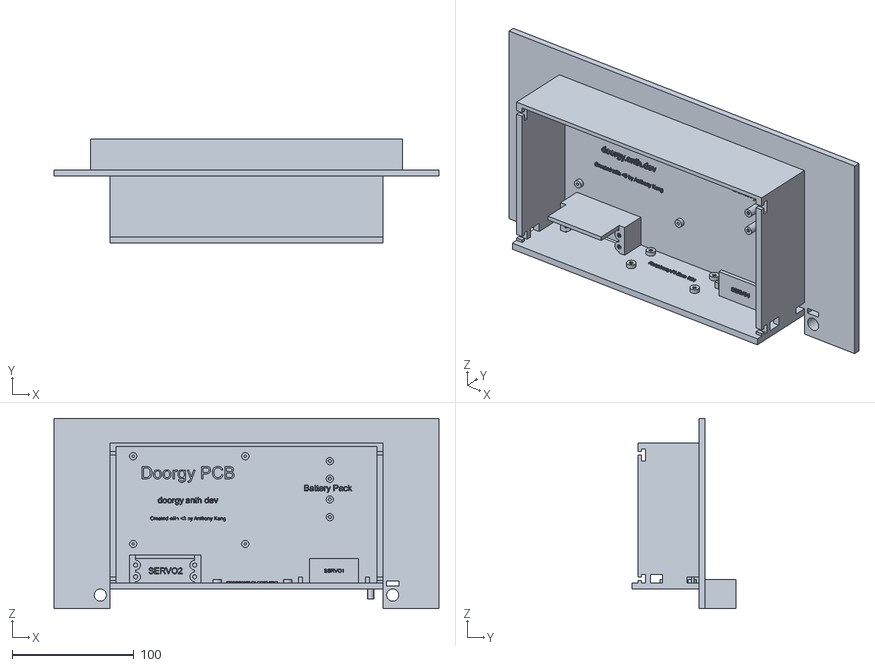
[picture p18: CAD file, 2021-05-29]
Doorgy Physical STL/Doorgy Interial Top Frame.stl
316.0 x 85.4 x 156.0

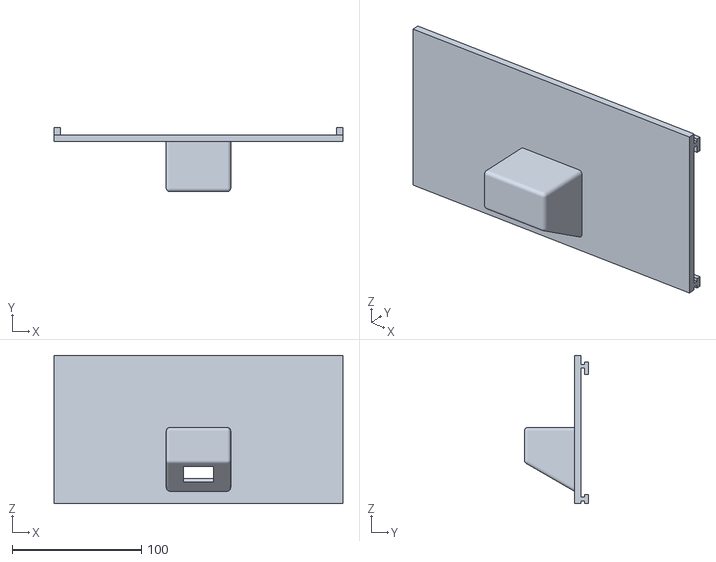
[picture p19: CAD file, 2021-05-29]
Doorgy Physical STL/Doorgy Interial Top Cover.stl
224.0 x 49.8 x 115.0

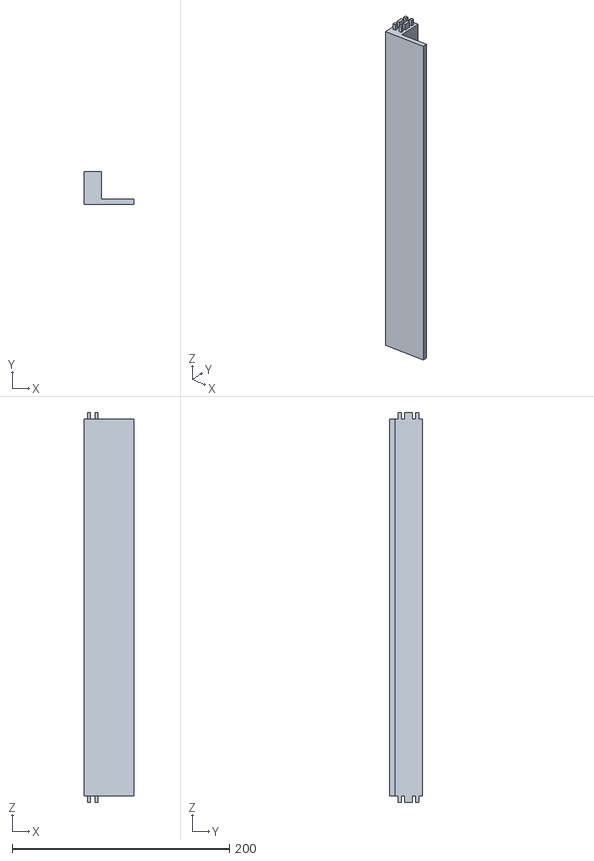
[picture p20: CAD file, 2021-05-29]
Doorgy Physical STL/Doorgy Interial Right Frame.stl
46.0 x 30.4 x 359.0

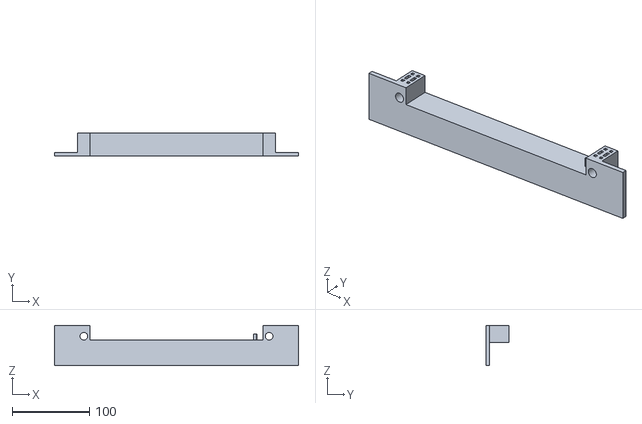
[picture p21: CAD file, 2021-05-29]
Doorgy Physical STL/Doorgy Interial Bottom Frame.stl
316.0 x 30.4 x 52.0

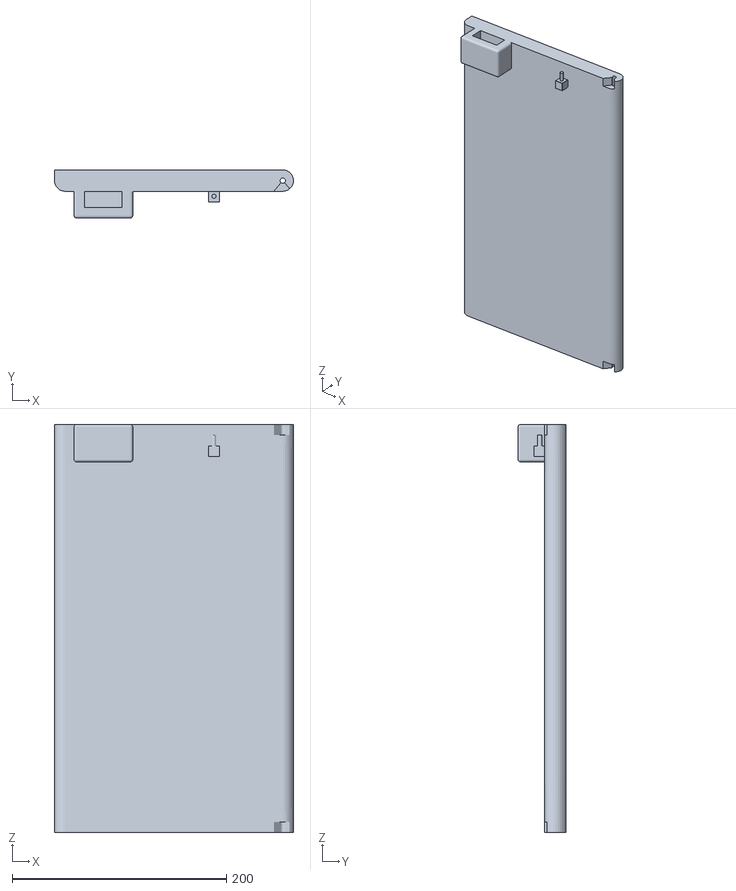
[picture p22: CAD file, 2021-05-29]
Doorgy Physical STL/Doorgy Door.stl
223.2 x 45.0 x 381.0

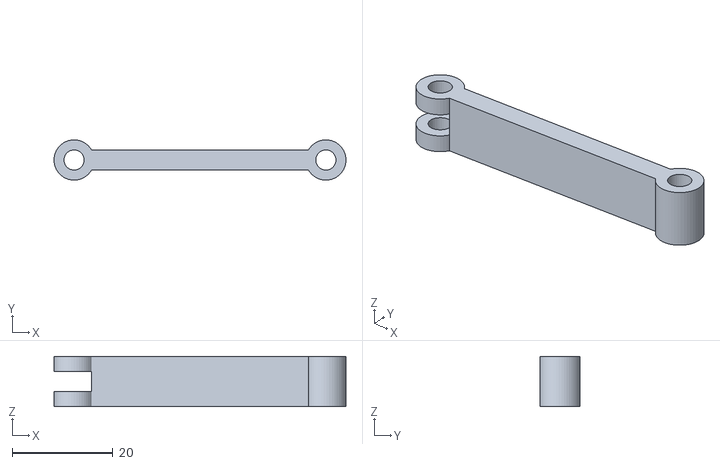
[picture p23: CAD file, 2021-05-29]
Doorgy Physical STL/Doorgy Door Connector.stl
58.0 x 8.00 x 10.0

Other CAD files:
Doorgy Physical STL/Doorgy Exterial Right Frame.stl
Doorgy Physical STL/Doorgy Interial Left Frame.stl

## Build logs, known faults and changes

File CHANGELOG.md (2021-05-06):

# Doorgy Change Log

- [Doorgy Change Log](#doorgy-change-log)
  - [v1.2.7](#v127)
  - [v1.2.6](#v126)
  - [v1.2.5](#v125)
  - [v1.2.4](#v124)
  - [v1.2.3](#v123)
  - [v1.2.2](#v122)
  - [v1.2.1](#v121)
  - [v1.2.0](#v120)
  - [v1.1.0](#v110)
  - [v1.0.0](#v100)

## v1.2.7

- Fix PCB Layout Drill Layer
- Fix PCB BOM Raspberry Pi Header
- Update README

## v1.2.6

- Update PCB Schematics and Layout

## v1.2.5

- Added draft PCB Schematics and Layout
- Added CHANGELOG.md

## v1.2.4

## v1.2.3

## v1.2.2

## v1.2.1

## v1.2.0

## v1.1.0

## v1.0.0

- Initial release
- Added doorgy.js

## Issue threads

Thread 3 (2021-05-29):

Project name might be misinterpreted

TheOneKevin, 2021-05-29:
The name Doorgy may be misinterpreted as the slang term "doorgy" may also have unpleasant and vulgar connotations. Instead, Doorgi might be a better alternative as it can be Door + Corgi.

Anthonykung, 2021-05-30:
Yes, we are aware of this issue however, that is after the PCB was created making the changes hard to implement. Changes will be made on 3.0.0 updates along with a new NPM listing.

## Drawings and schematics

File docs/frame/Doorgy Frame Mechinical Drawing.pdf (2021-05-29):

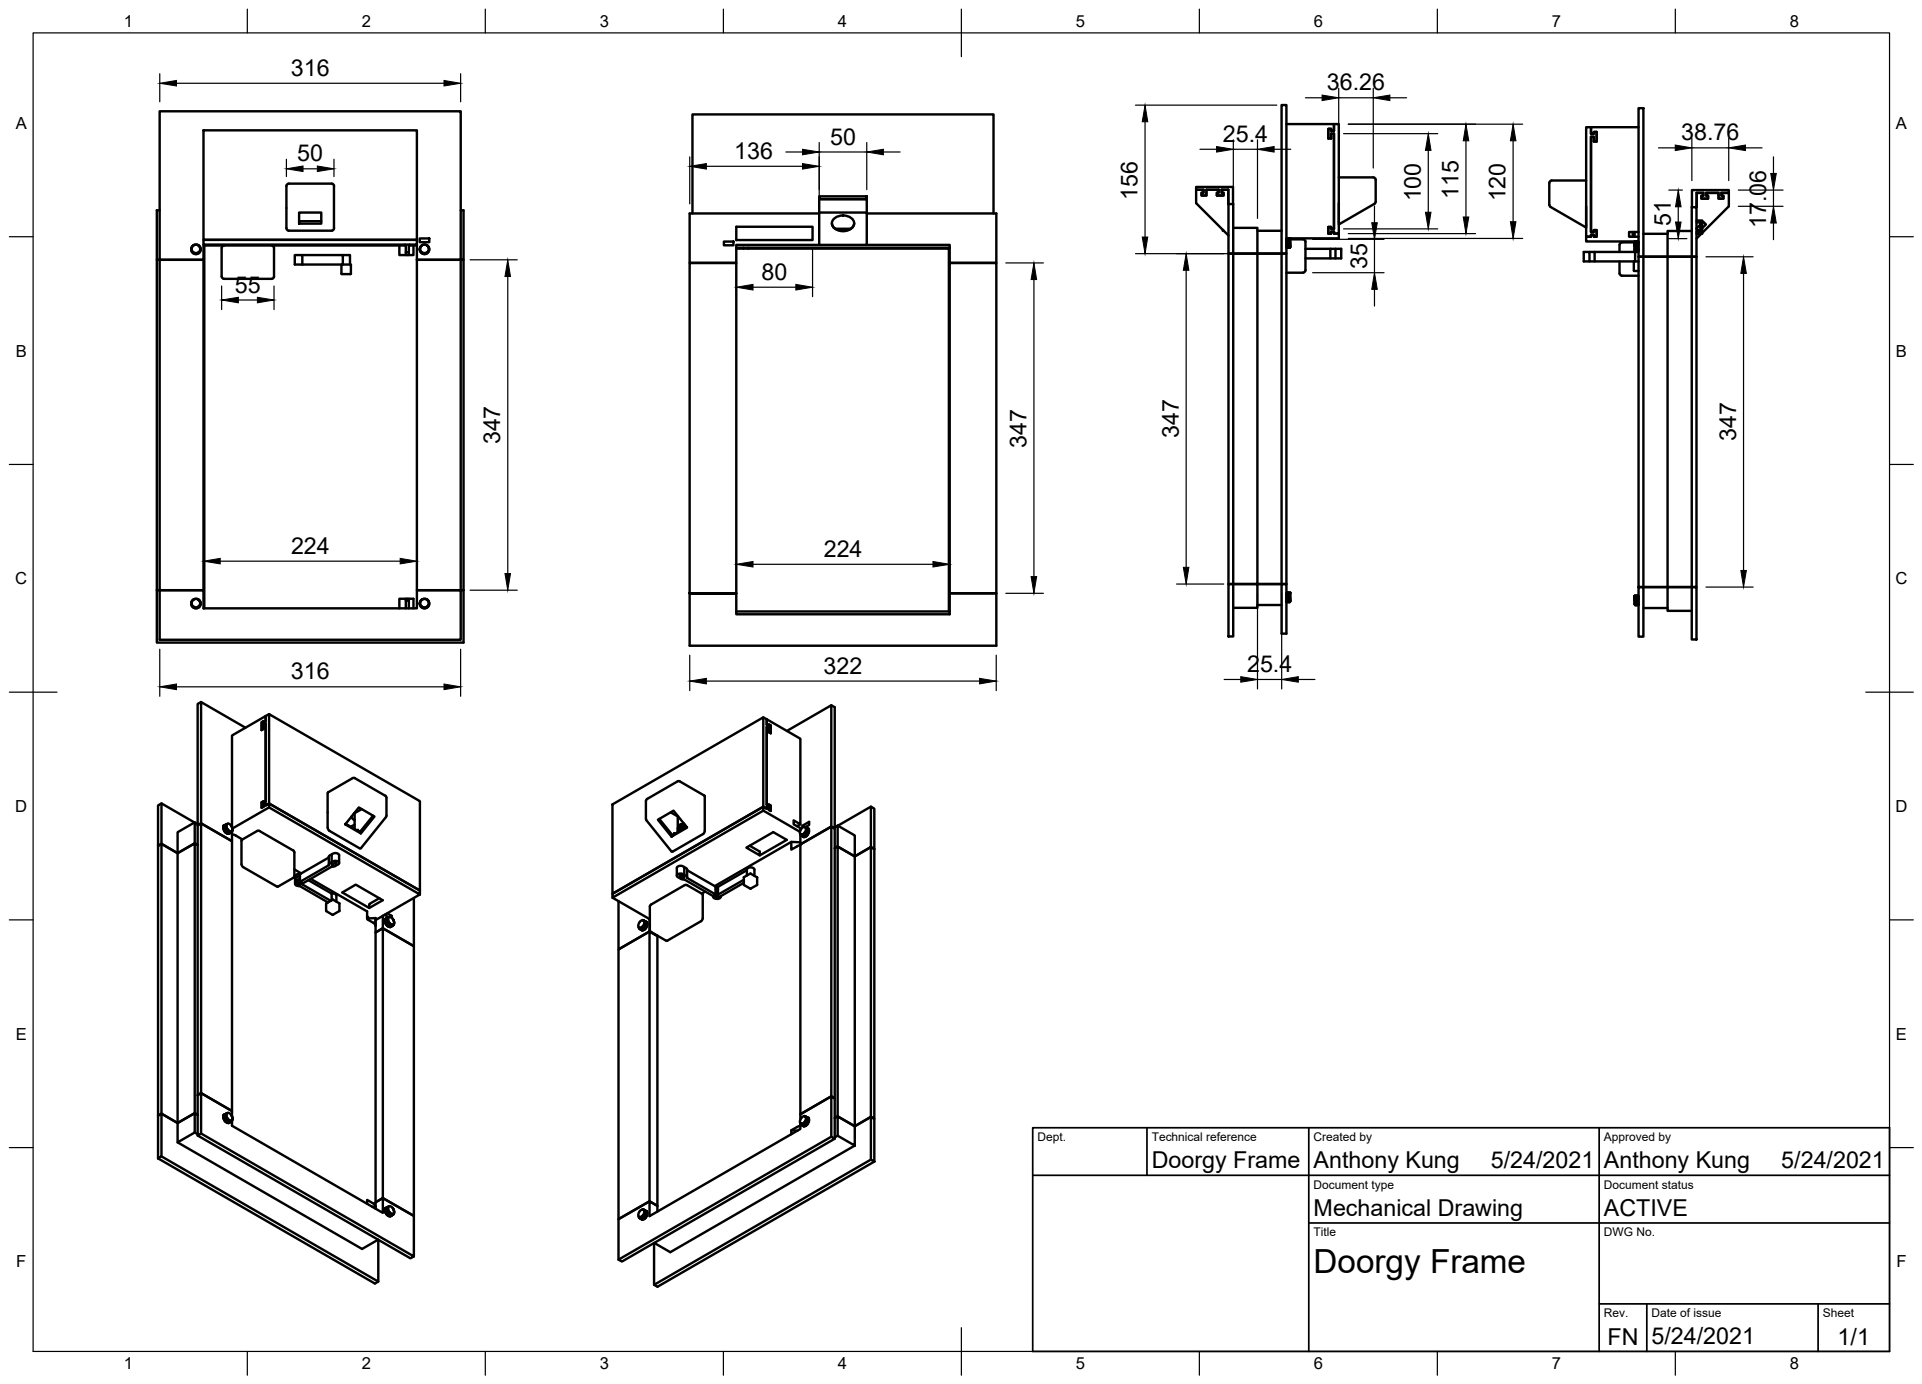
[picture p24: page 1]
Title; DWG No.; Rev.; Date of issue; Sheet; Doorgy Frame

Dept. | Technical reference Doorgy Frame | Created by Anthony Kung 5/24/2021 | Approved by Anthony Kung 5/24/2021

Document type Mechanical Drawing | Document status ACTIVE

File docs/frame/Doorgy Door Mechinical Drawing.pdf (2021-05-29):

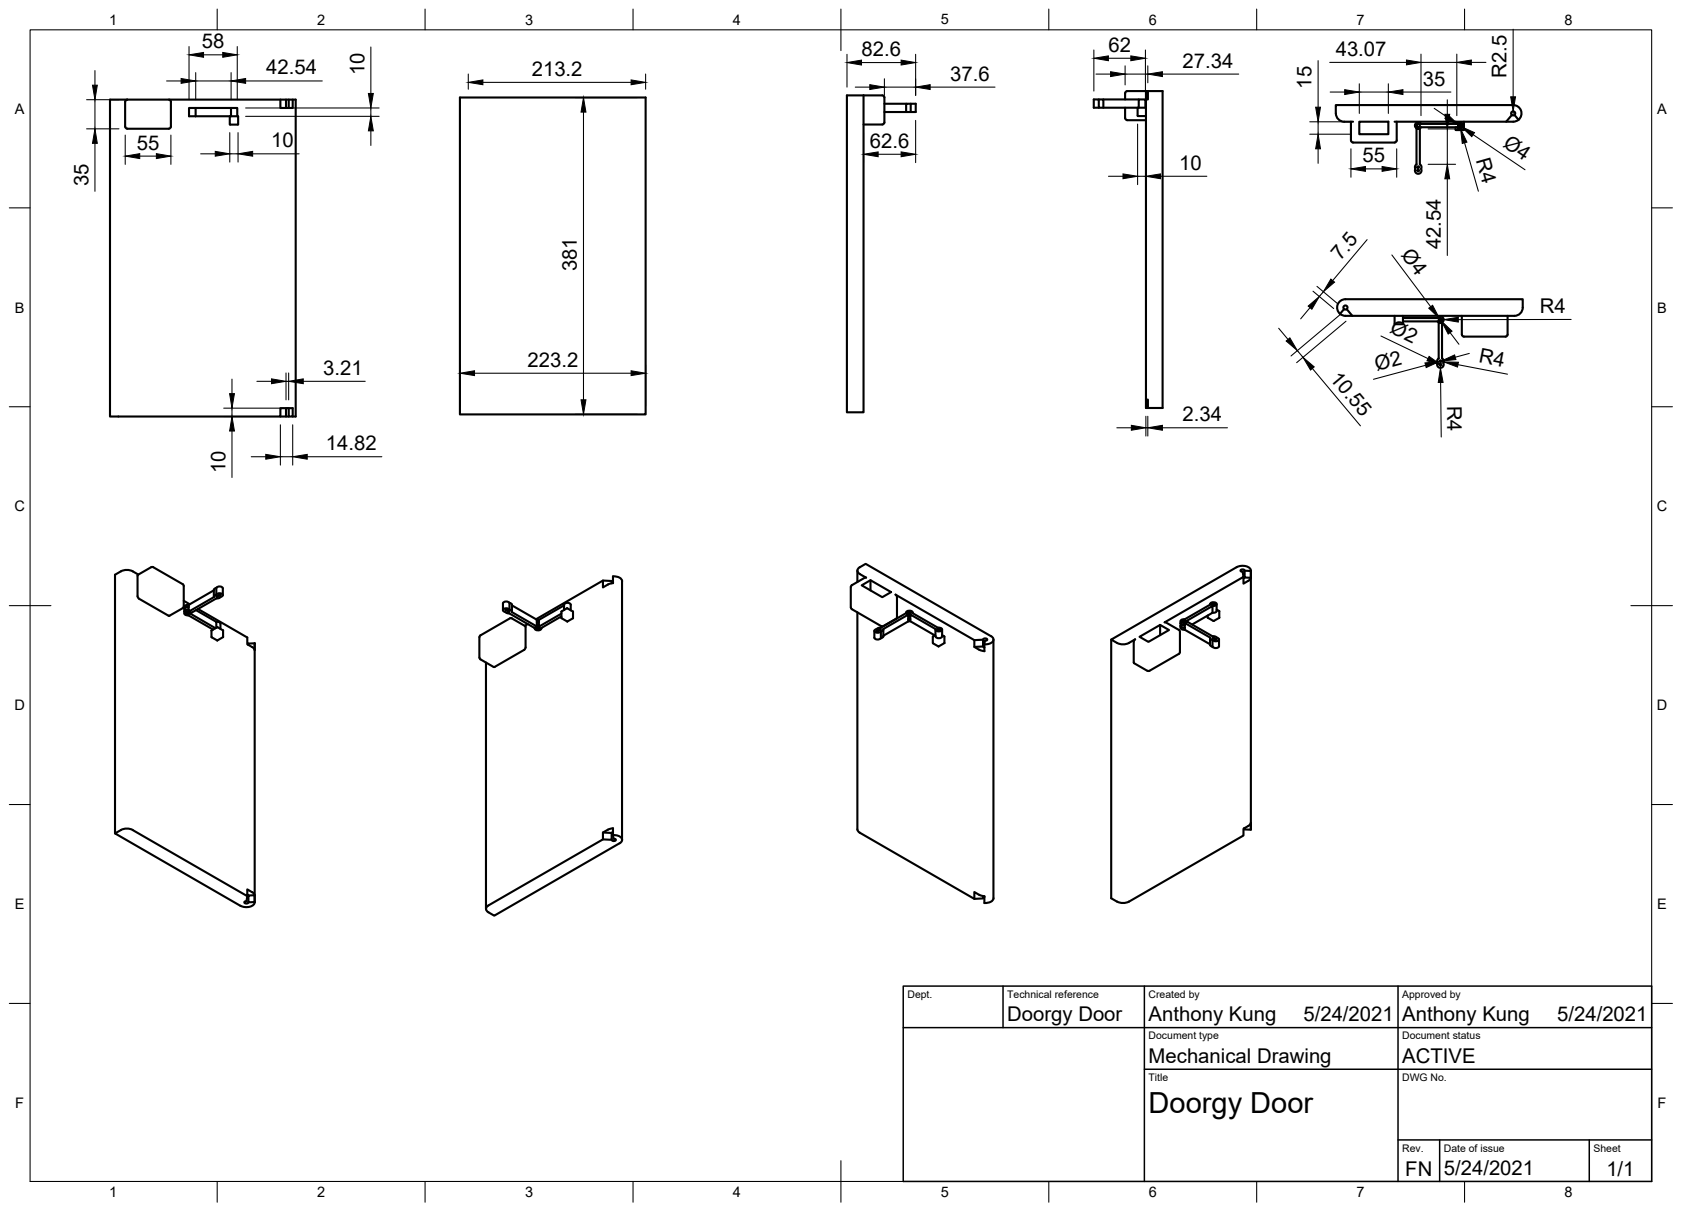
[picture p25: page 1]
Title; DWG No.; Rev.; Date of issue; Sheet; Doorgy Door

Dept. | Technical reference Doorgy Door | Created by Anthony Kung 5/24/2021 | Approved by Anthony Kung 5/24/2021

Document type Mechanical Drawing | Document status ACTIVE

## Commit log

2021-04-27 fix file copy error
    [doorgy.js]
2021-04-27 Update pin num
2021-04-27 fix pin num
2021-04-27 fix wrong pin
2021-05-01 Added draft PCB Schematics and Layout
2021-05-05 Updated PCB Docs
    - Update Schematic to v22
    - Update Routing to v32
    - Added Gerber Files
    - Added BOM
    - Added CPL
    - Added PCB Rendering
    [Doorgy-PCB-BOM.xlsx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]
2021-05-06 v1.2.7 update
    - Fix PCB Layout Drill Layer
    - Fix PCB BOM Raspberry Pi Header
    - Update README
    [Doorgy PCB BOM.xlsx, Doorgy-PCB-BOM.xlsx]
2021-05-07 Update IO docs for print
2021-05-26 fix timer issue
2021-05-26 fix crashing from json error
    [doorgy.js]
2021-05-28 fix file copy errors
    [doorgy.js]
2021-05-28 fixed servo duplicated operations
    [doorgy.js]
2021-05-28 fixed primary operation and added logs
    [doorgy.js]
2021-05-28 fixed primary operation condition
    [doorgy.js]
2021-05-28 fixed open function condition
    [doorgy.js]
2021-05-28 fix opening condition error
    [doorgy.js]
2021-05-28 fixed unlock logic and open direction
    [doorgy.js]
2021-05-28 fixed init and network lost
    [doorgy.js]
2021-05-29 added config utility
    [Doorgy Door Connector.stl, Doorgy Door.stl, Doorgy Exterial Bottom Frame.stl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]
